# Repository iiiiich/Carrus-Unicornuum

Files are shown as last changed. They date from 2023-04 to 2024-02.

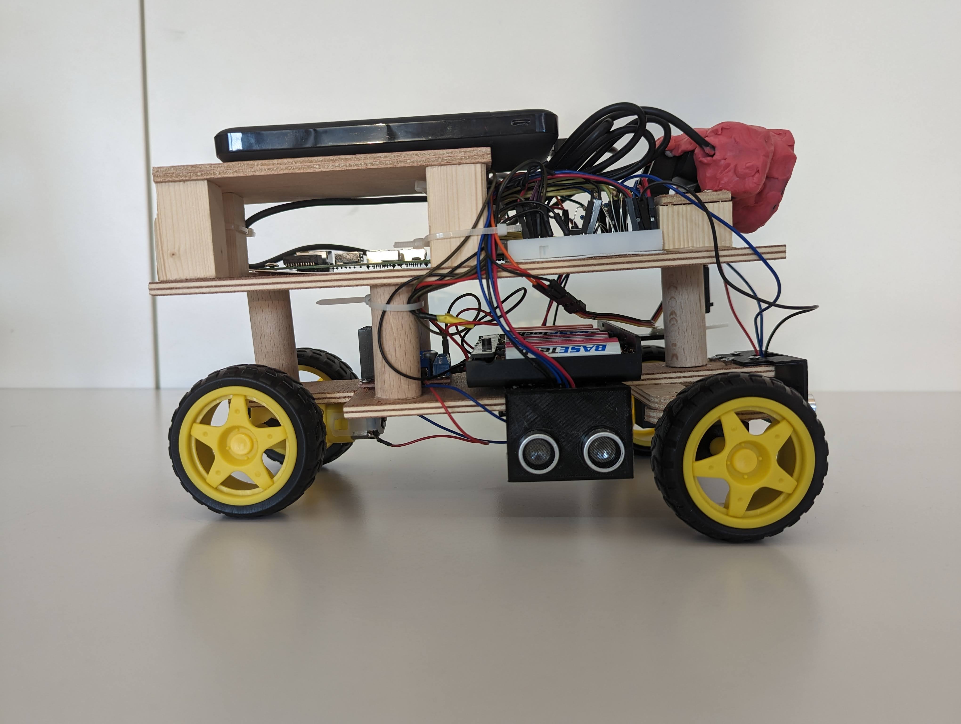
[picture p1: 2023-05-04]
Roboterauto/Ansicht rechts.JPG

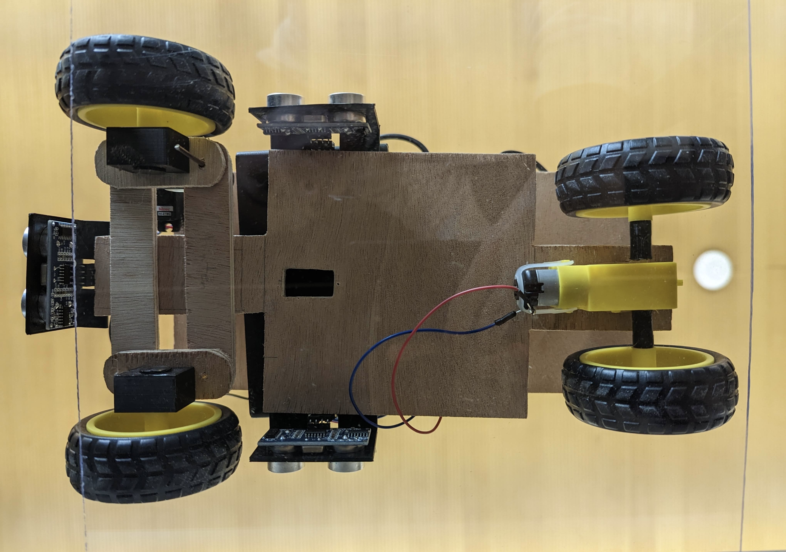
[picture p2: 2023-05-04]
Roboterauto/Ansicht unten.jpg

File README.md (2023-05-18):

# Carrus Unicornuum
World Robot Olympiad 2023 Future Engineers

## Ordnerstruktur
- Im Ordner `3D-Modelle` befindet sich eine .step-Datei, in der alle 3D-Modelle von 3D-gedruckten Komponenten des Roboters zu finden sind.
- Im Ordner `Programmcode` befindet sich der Code, der vom Roboter zum autonomen Fahren verwendet wird, sowie anderer Code, der zur Umsetzung benötigt wird.
- Im Ordner `Roboterauto` befinden sich sechs Fotos des Roboters, die ihn von allen Seiten zeigen.
- Im Ordner `Schaltpläne` befindet sich ein Schaltplan, auf dem zu erkenn ist, wie die einzelnen Komponenten miteinander verbunden sind.
- Im Ordner `Technische Zeichnungen` befinden sich technische Zeichnungen von 3D-gedruckten Komponenten des Roboterautos.
- Im Ordner `Video` befinden sich zwei Links zu YouTube-Videos, die den Roboter bei der autonomen Fahrt sowohl beim Eröffnungs- als auch beim Hindernisrennen zeigen.

## Hardware
### Motorisierung
Der Antrieb des Roboterautos geschieht durch einen DC-Motor. Dieser ist über ein Getriebe mit der Hinterachse und somit mit den Rädern verbunden. Die Lenkung geschieht unabhängig vom Antrieb mit Hilfe eines Servo-Motors des Typs HS-81MG und läuft über die Vorderachse. Alle Motoren sind mit einem Motortreiber L298N verbunden. Dieser regelt die Stromversorgung der Motoren.

### Energie
Die Energieversorgung des Roboterautos geschieht über zwei Einheiten. Zum einen wird der Motortreiber von einer Batterie-Box mit 8 Batterien des Typs AA betrieben. Der Raspberry Pi wird hingegen von einer Powerbank (5V, 3A out; ca. 10.000 mAh) mit Strom versorgt.

### Sensoren
Das Roboter-Auto verfügt neben einer Kamera mit Weitwinkellinse auch über 3 Ultraschallsensoren (HC-SR04), welche dazu dienen, den Abstand nach vorne und zu den Wänden zu bemessen. Somit kann die Lage des Roboterautos innerhalb des Parcours ermittelt werden. Die Kamera hingegen bestimmt den Abstand und die Farbe von Hindernissen.  

## Software
### Eröffnungsrennen
#### Kurven
Flussdiagramm zum Kurvenfahren
#### Korrekturen
Flussdiagramm zum Korrigieren

### Hindernisrennen
Flussdiagramm zur Hindernisumfahrung

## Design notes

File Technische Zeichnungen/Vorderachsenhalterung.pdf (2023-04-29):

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

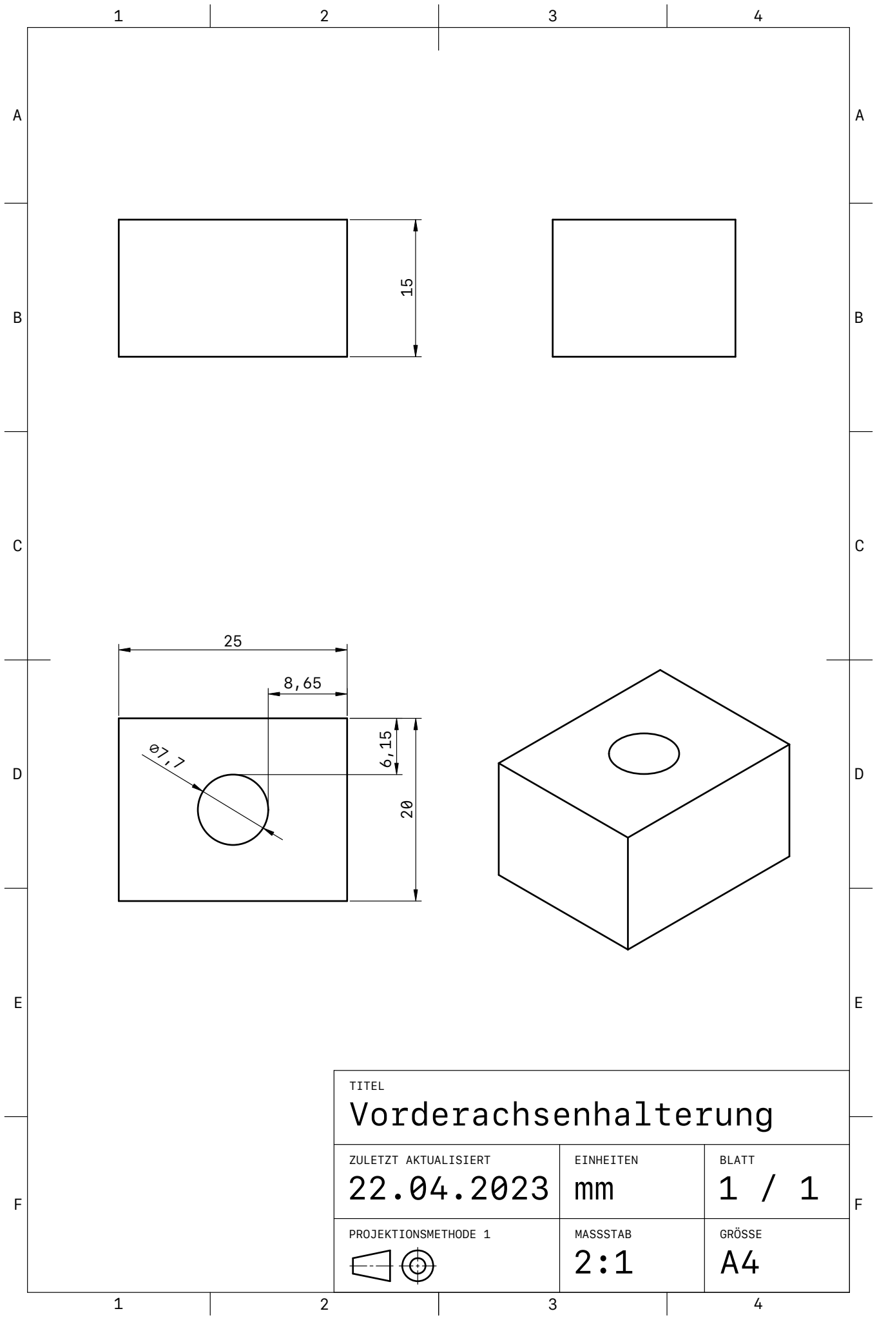
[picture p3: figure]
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

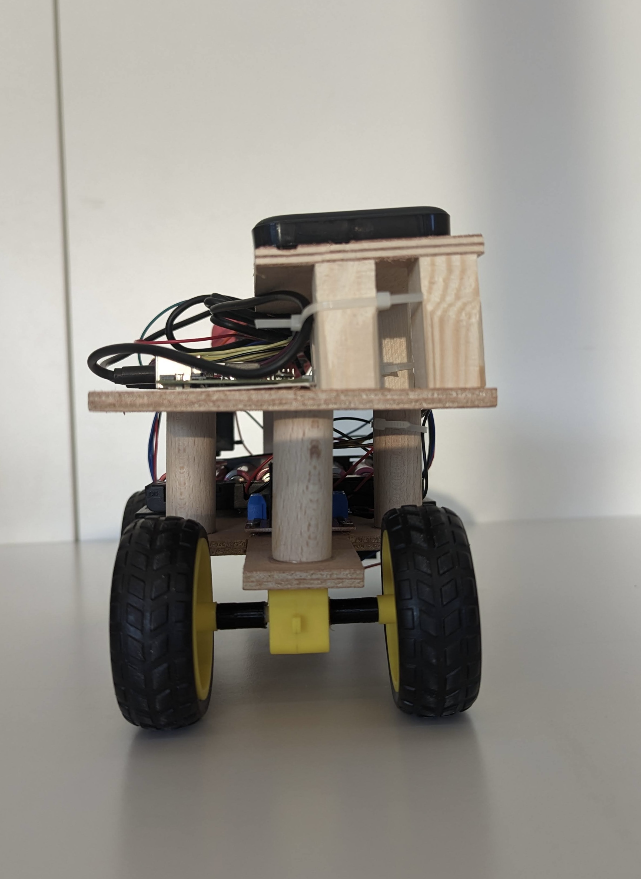
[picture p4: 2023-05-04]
Roboterauto/Ansicht hinten.jpg

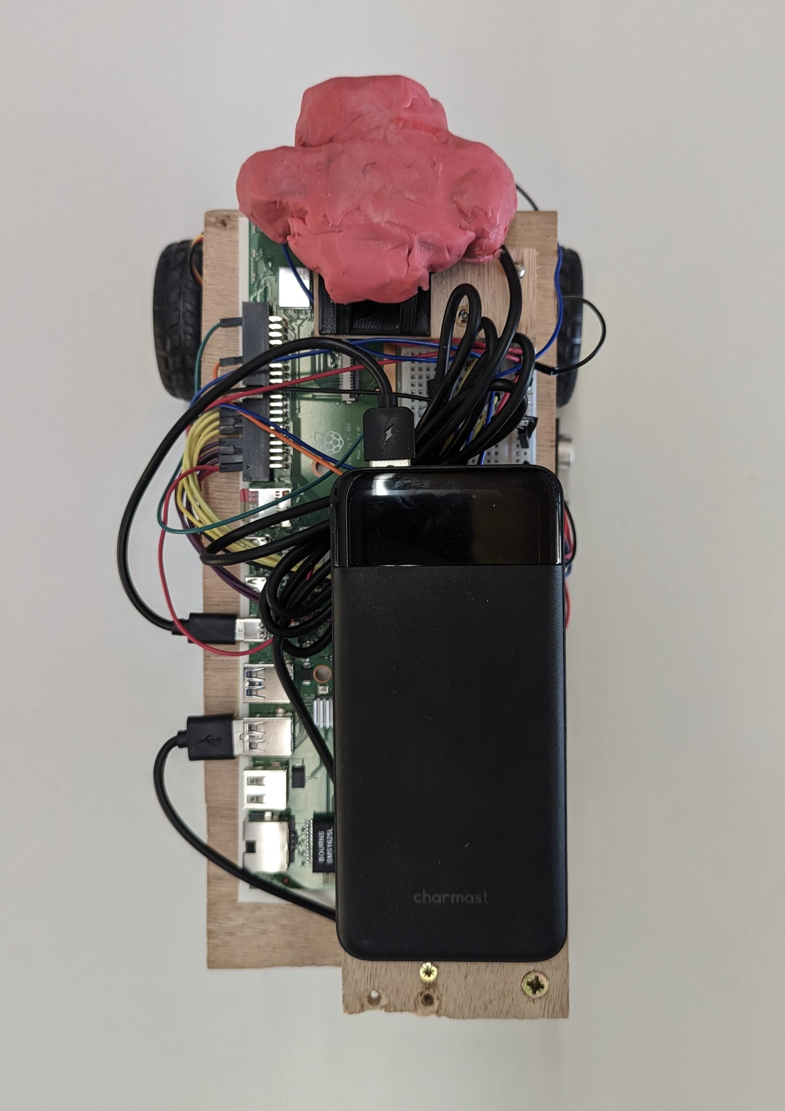
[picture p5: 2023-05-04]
Roboterauto/Ansicht oben.jpg

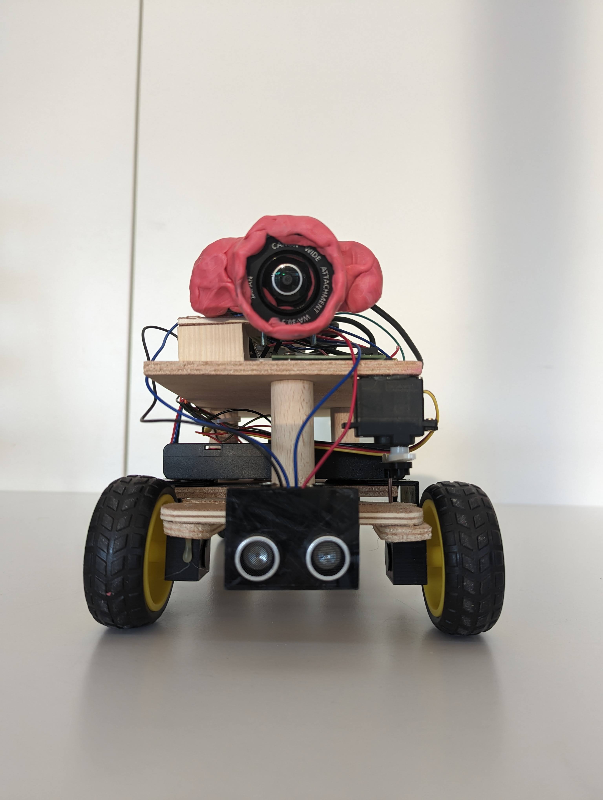
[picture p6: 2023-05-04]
Roboterauto/Ansicht vorne.JPG

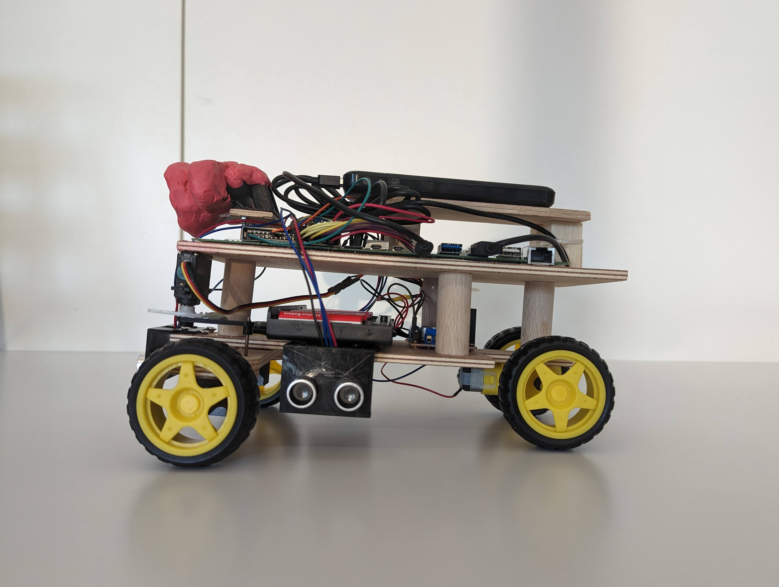
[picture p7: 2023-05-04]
Roboterauto/Ansicht links.JPG

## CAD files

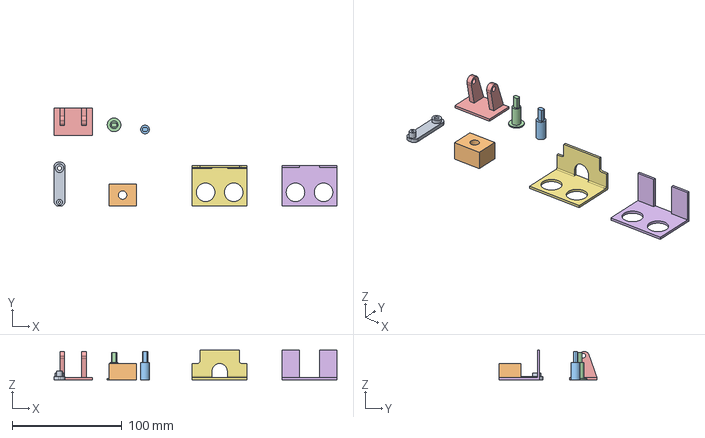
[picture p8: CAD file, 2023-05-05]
3D-Modelle/3D-Modelle.step
257.5 x 89.3 x 27.0 mm

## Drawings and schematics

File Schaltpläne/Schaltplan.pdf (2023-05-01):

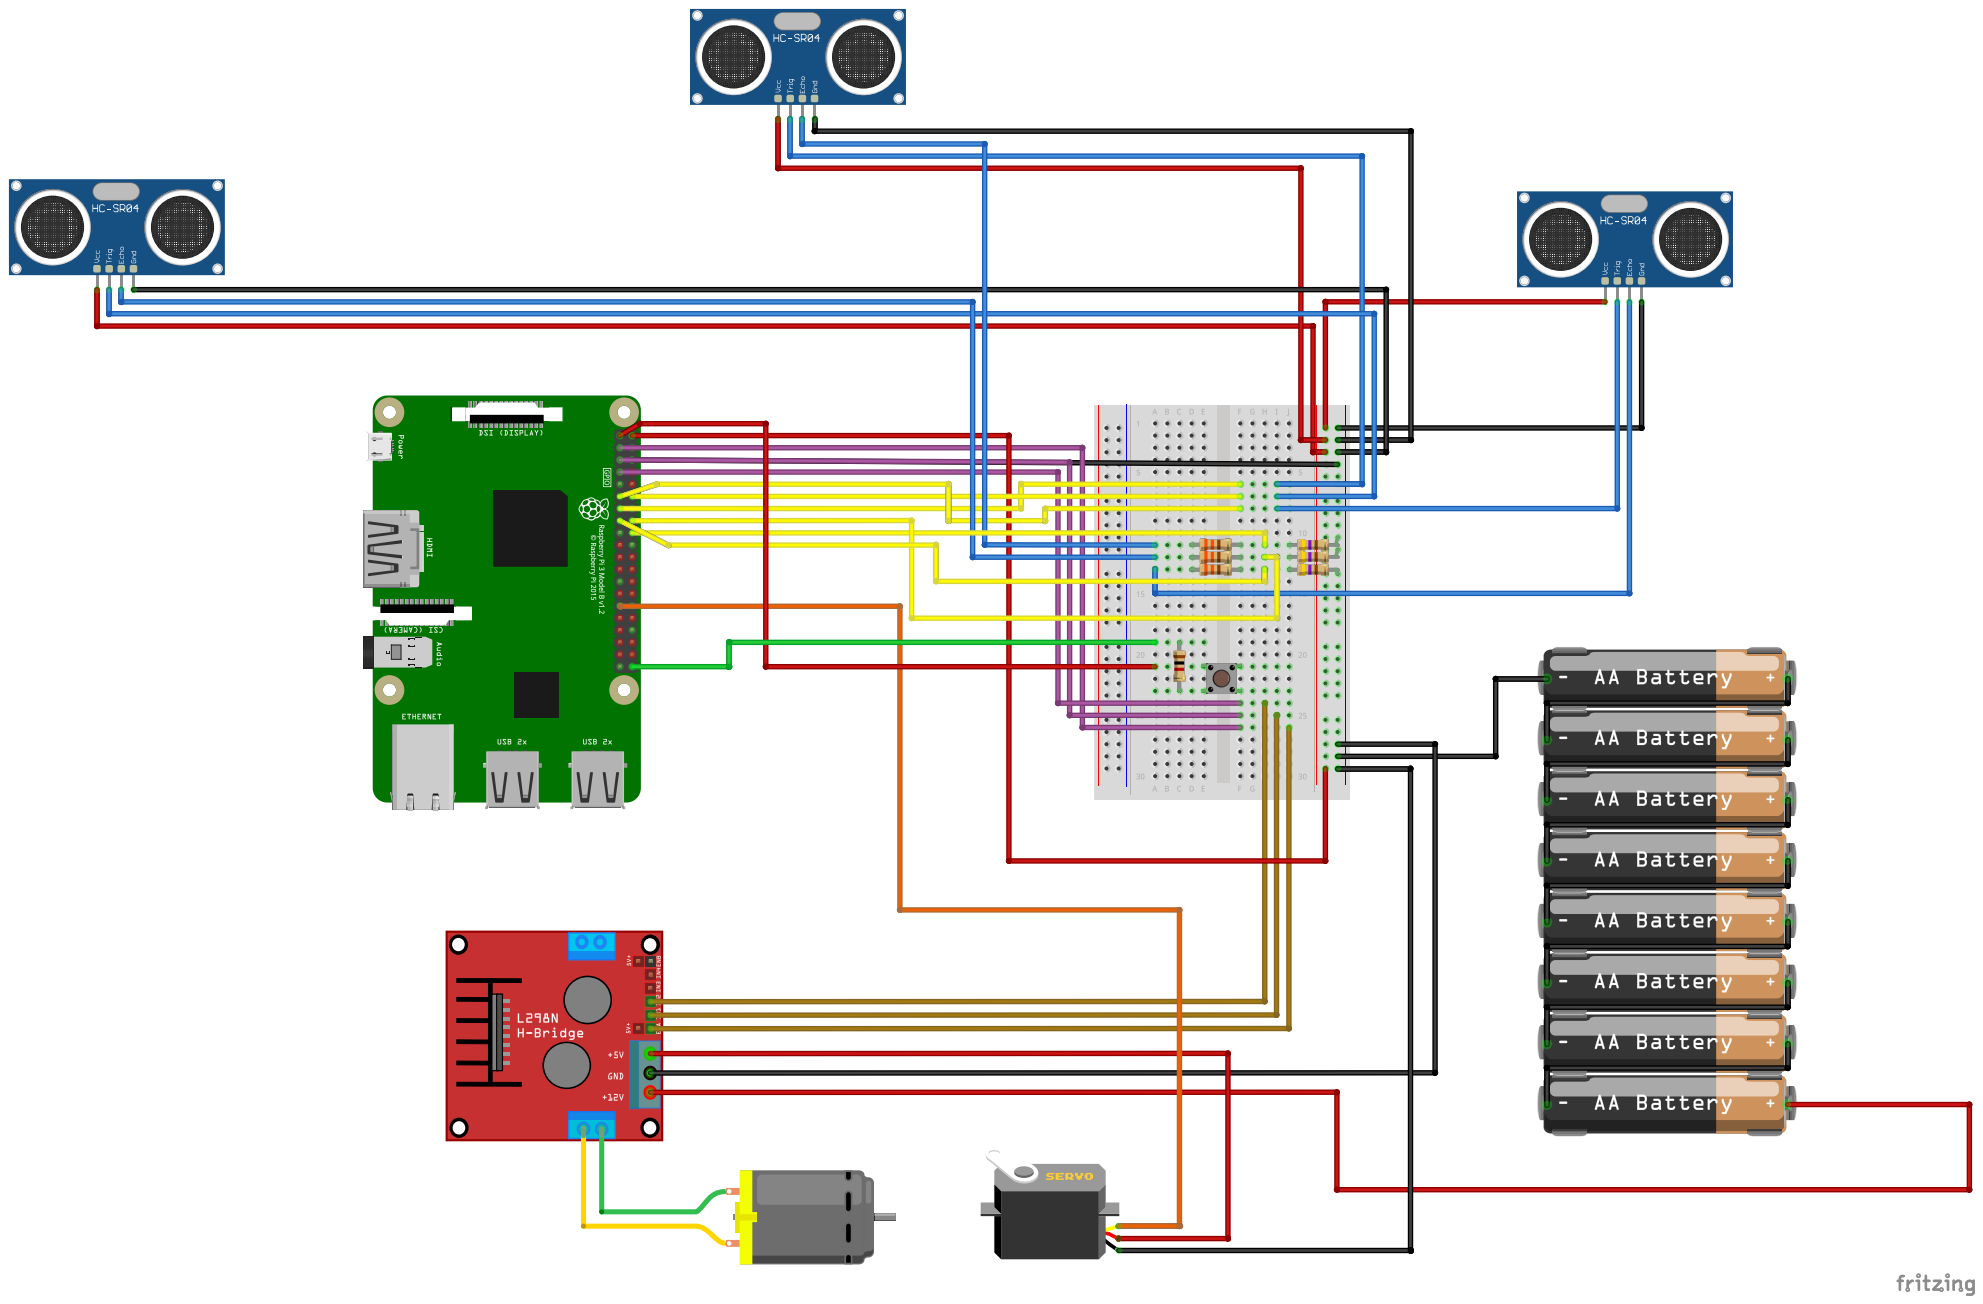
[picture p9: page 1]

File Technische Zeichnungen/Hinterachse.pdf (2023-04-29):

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

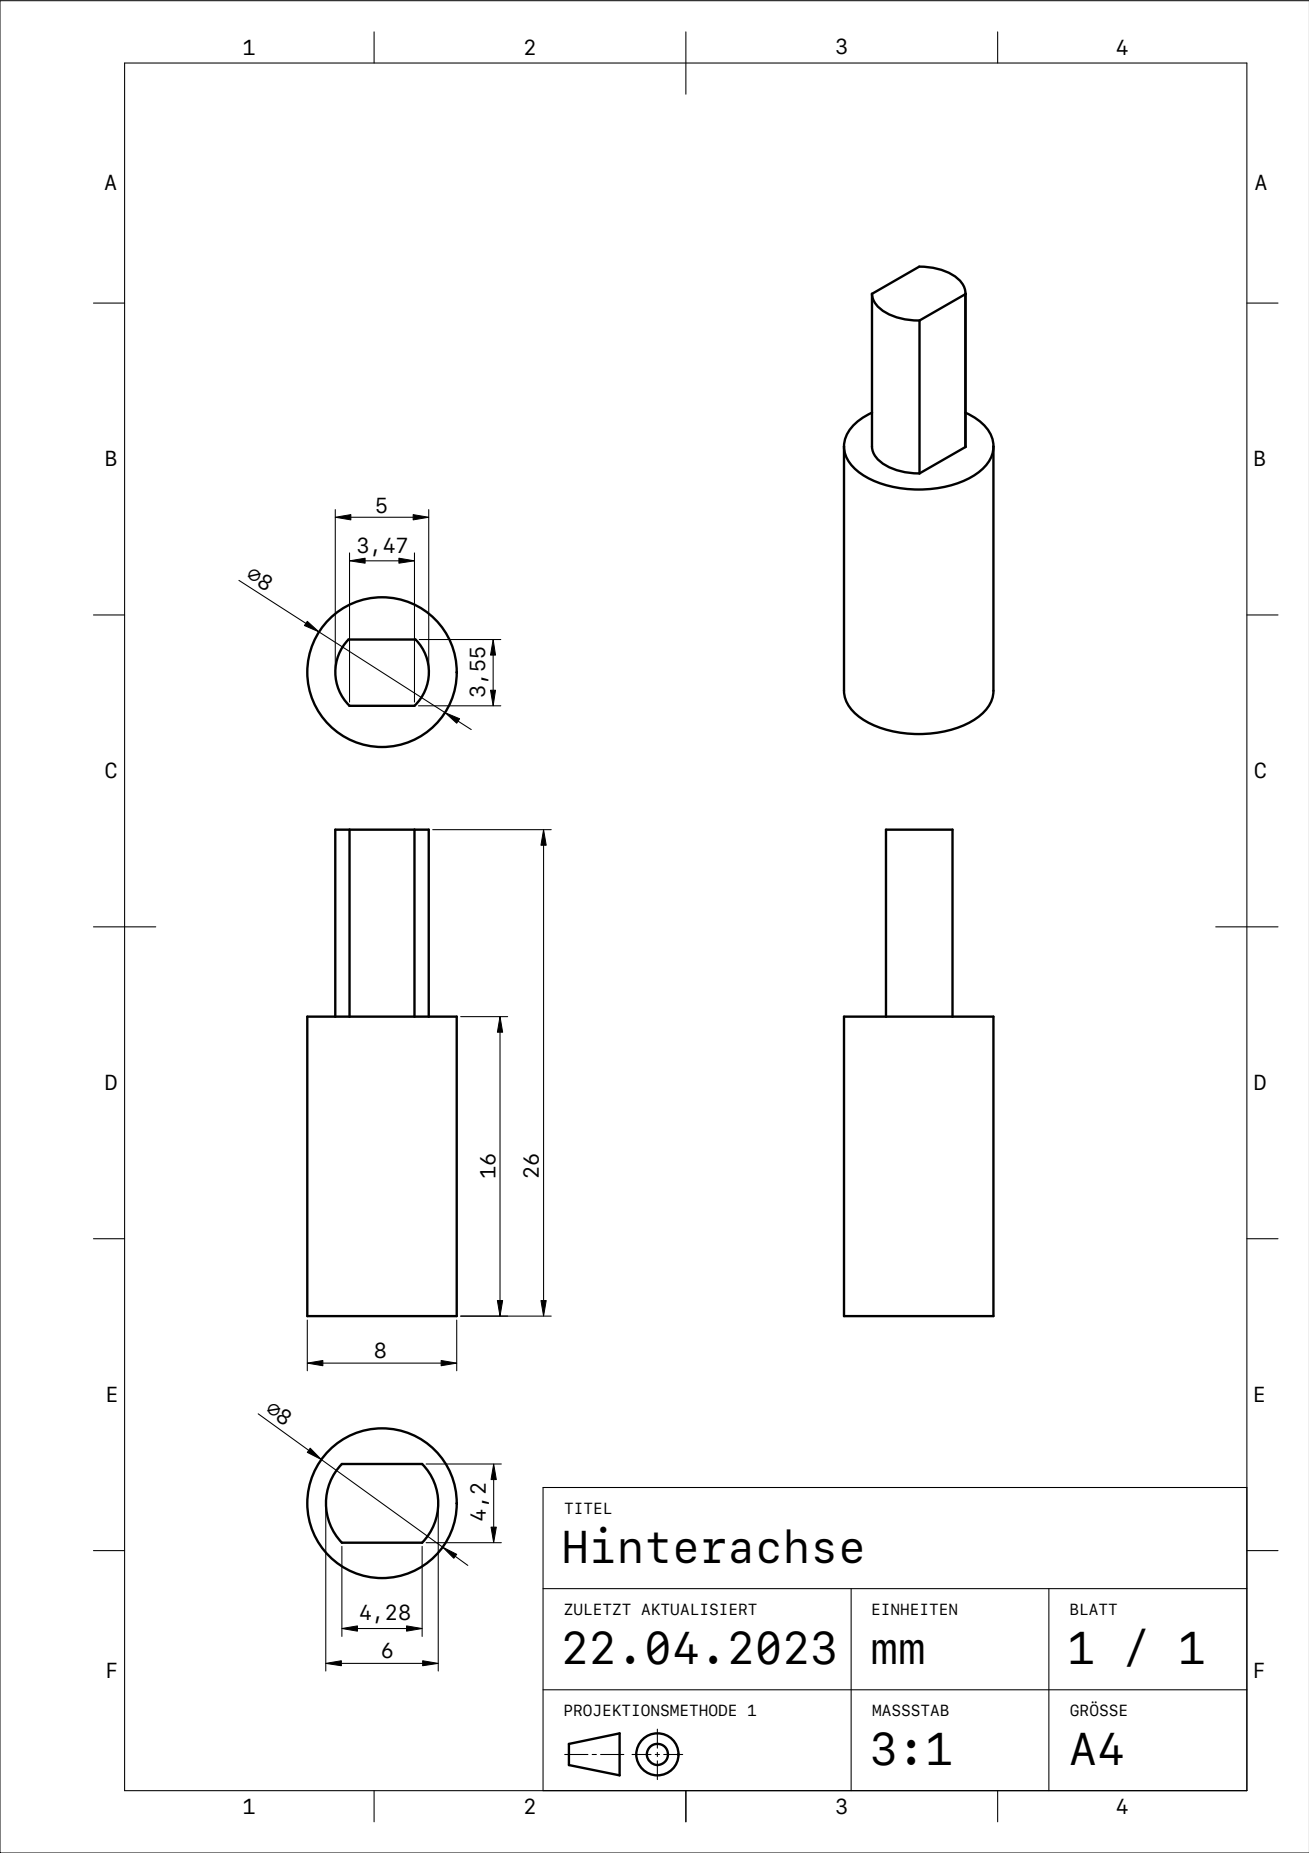
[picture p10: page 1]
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

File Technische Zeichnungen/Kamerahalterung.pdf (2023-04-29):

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

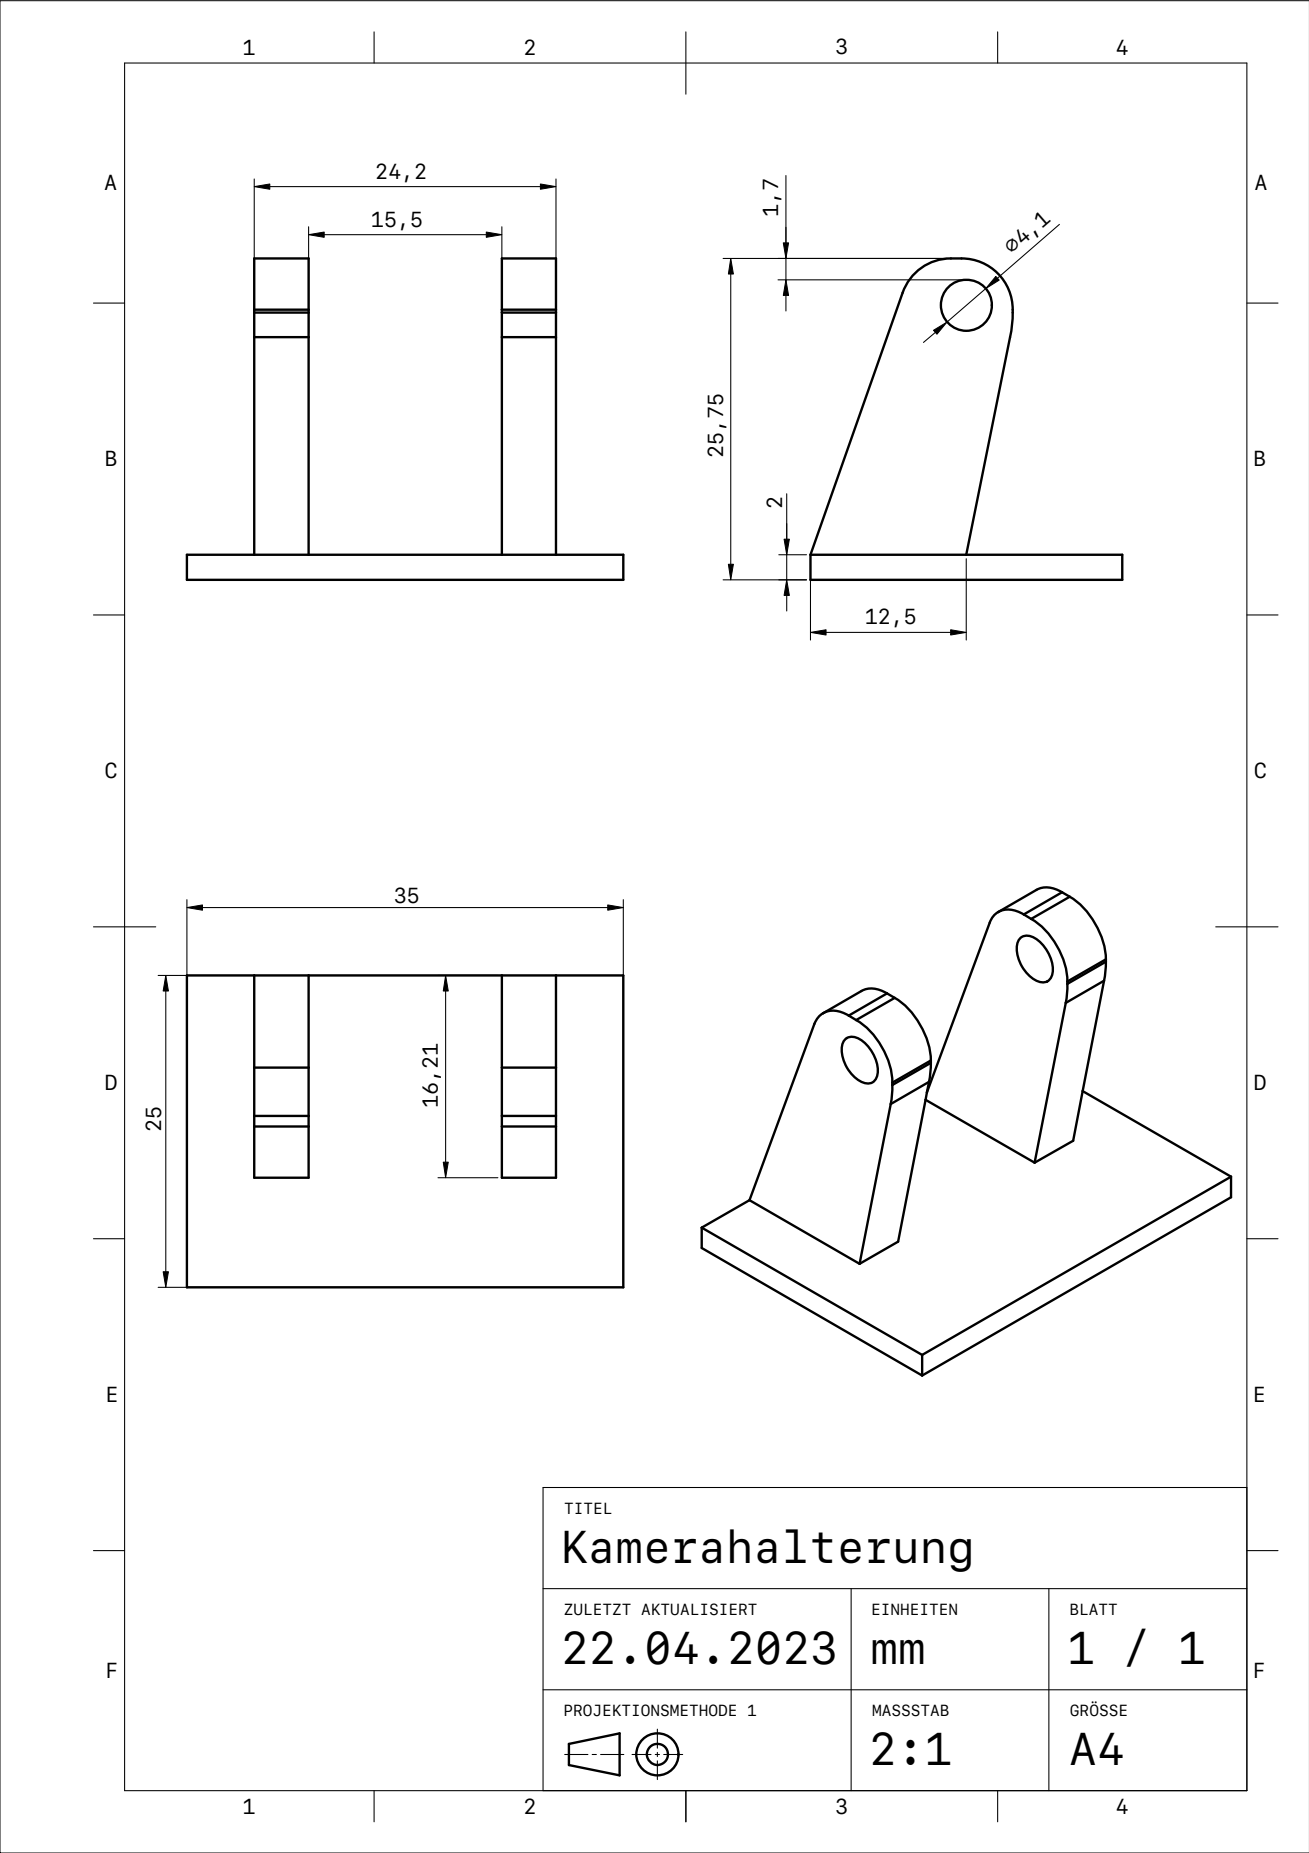
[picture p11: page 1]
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

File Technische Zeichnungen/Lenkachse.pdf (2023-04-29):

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

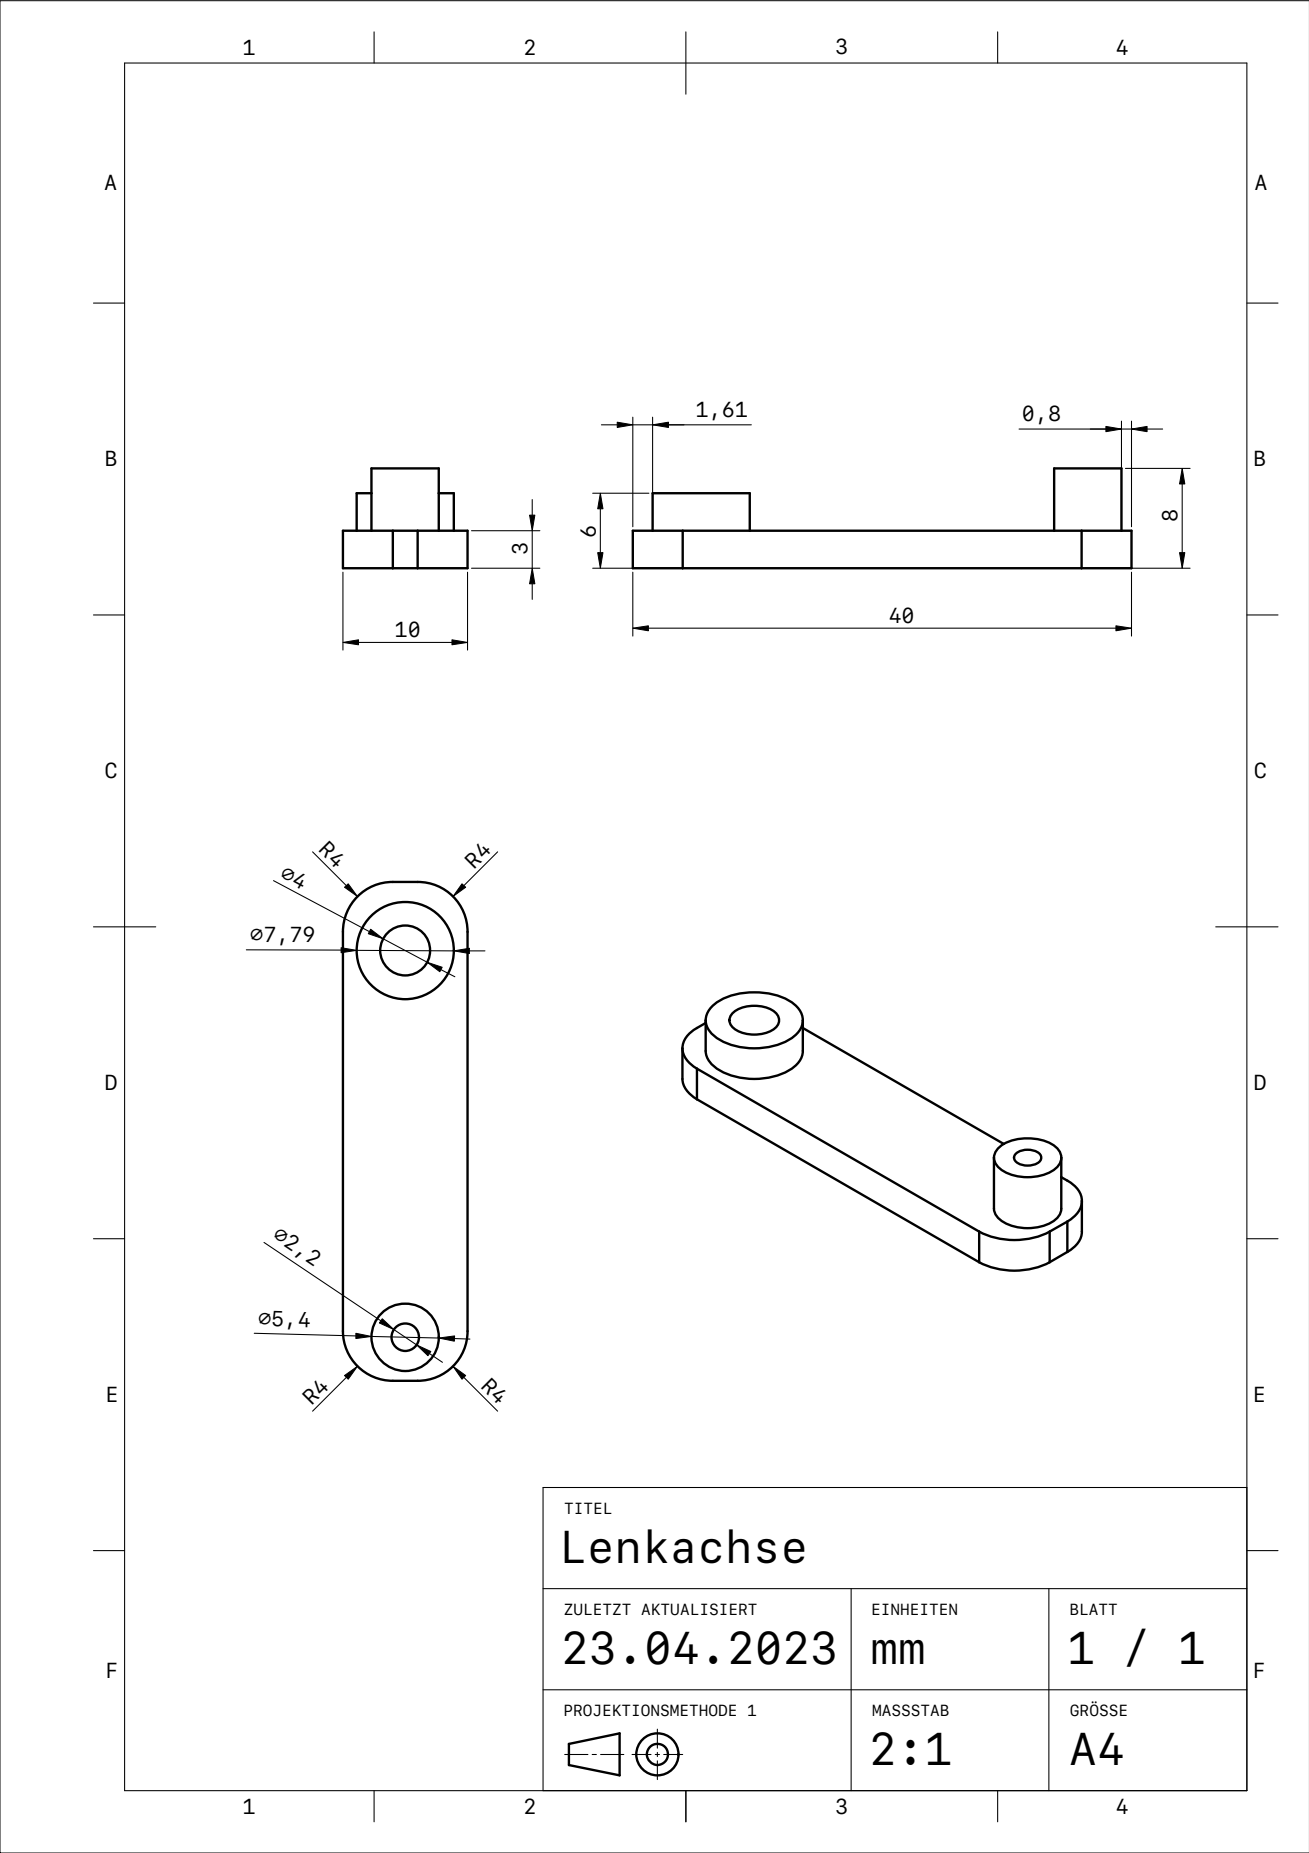
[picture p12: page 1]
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

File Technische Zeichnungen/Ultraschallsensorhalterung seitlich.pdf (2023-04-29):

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

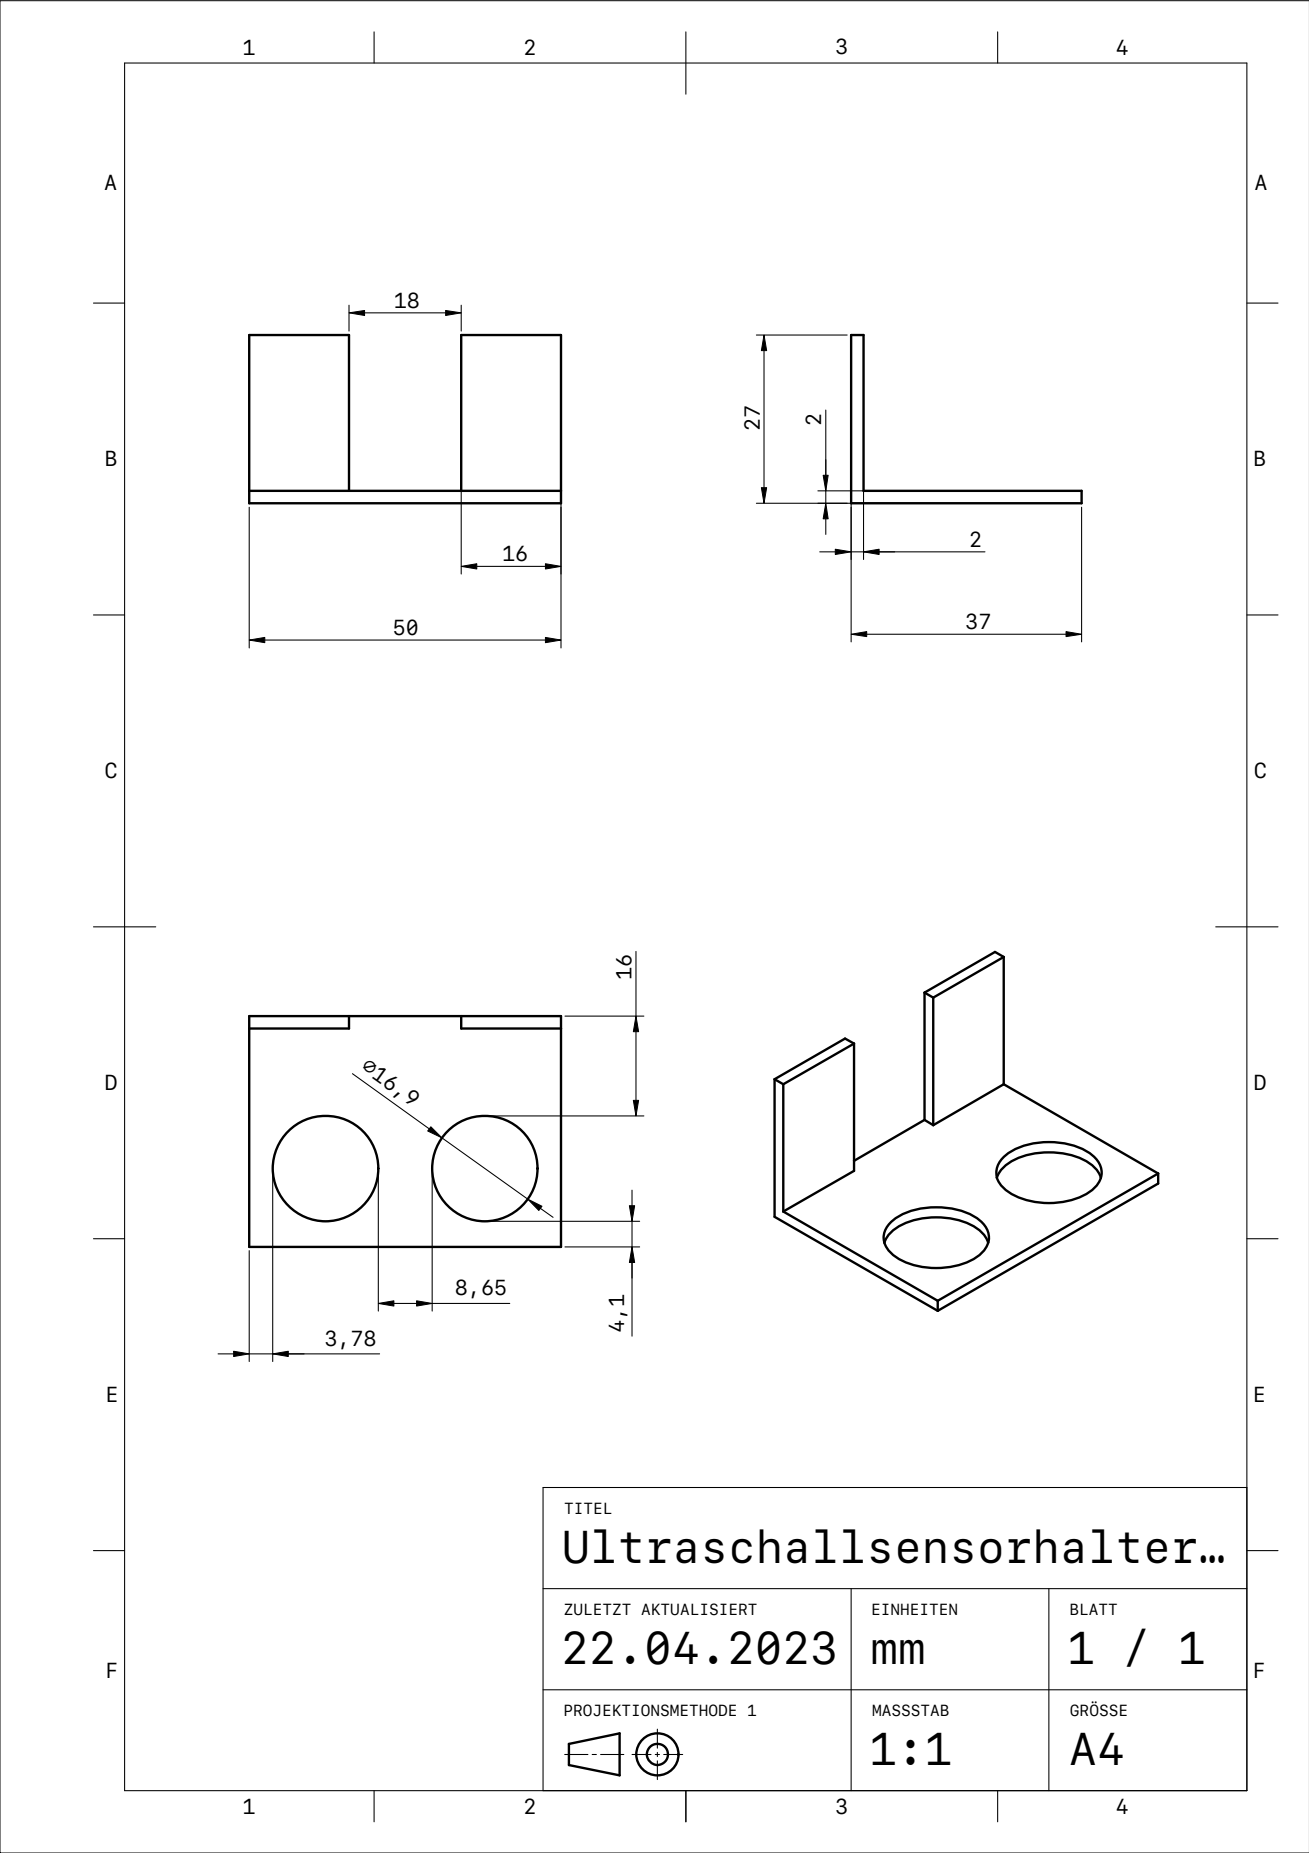
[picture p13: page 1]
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

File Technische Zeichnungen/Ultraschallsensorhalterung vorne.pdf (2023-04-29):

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

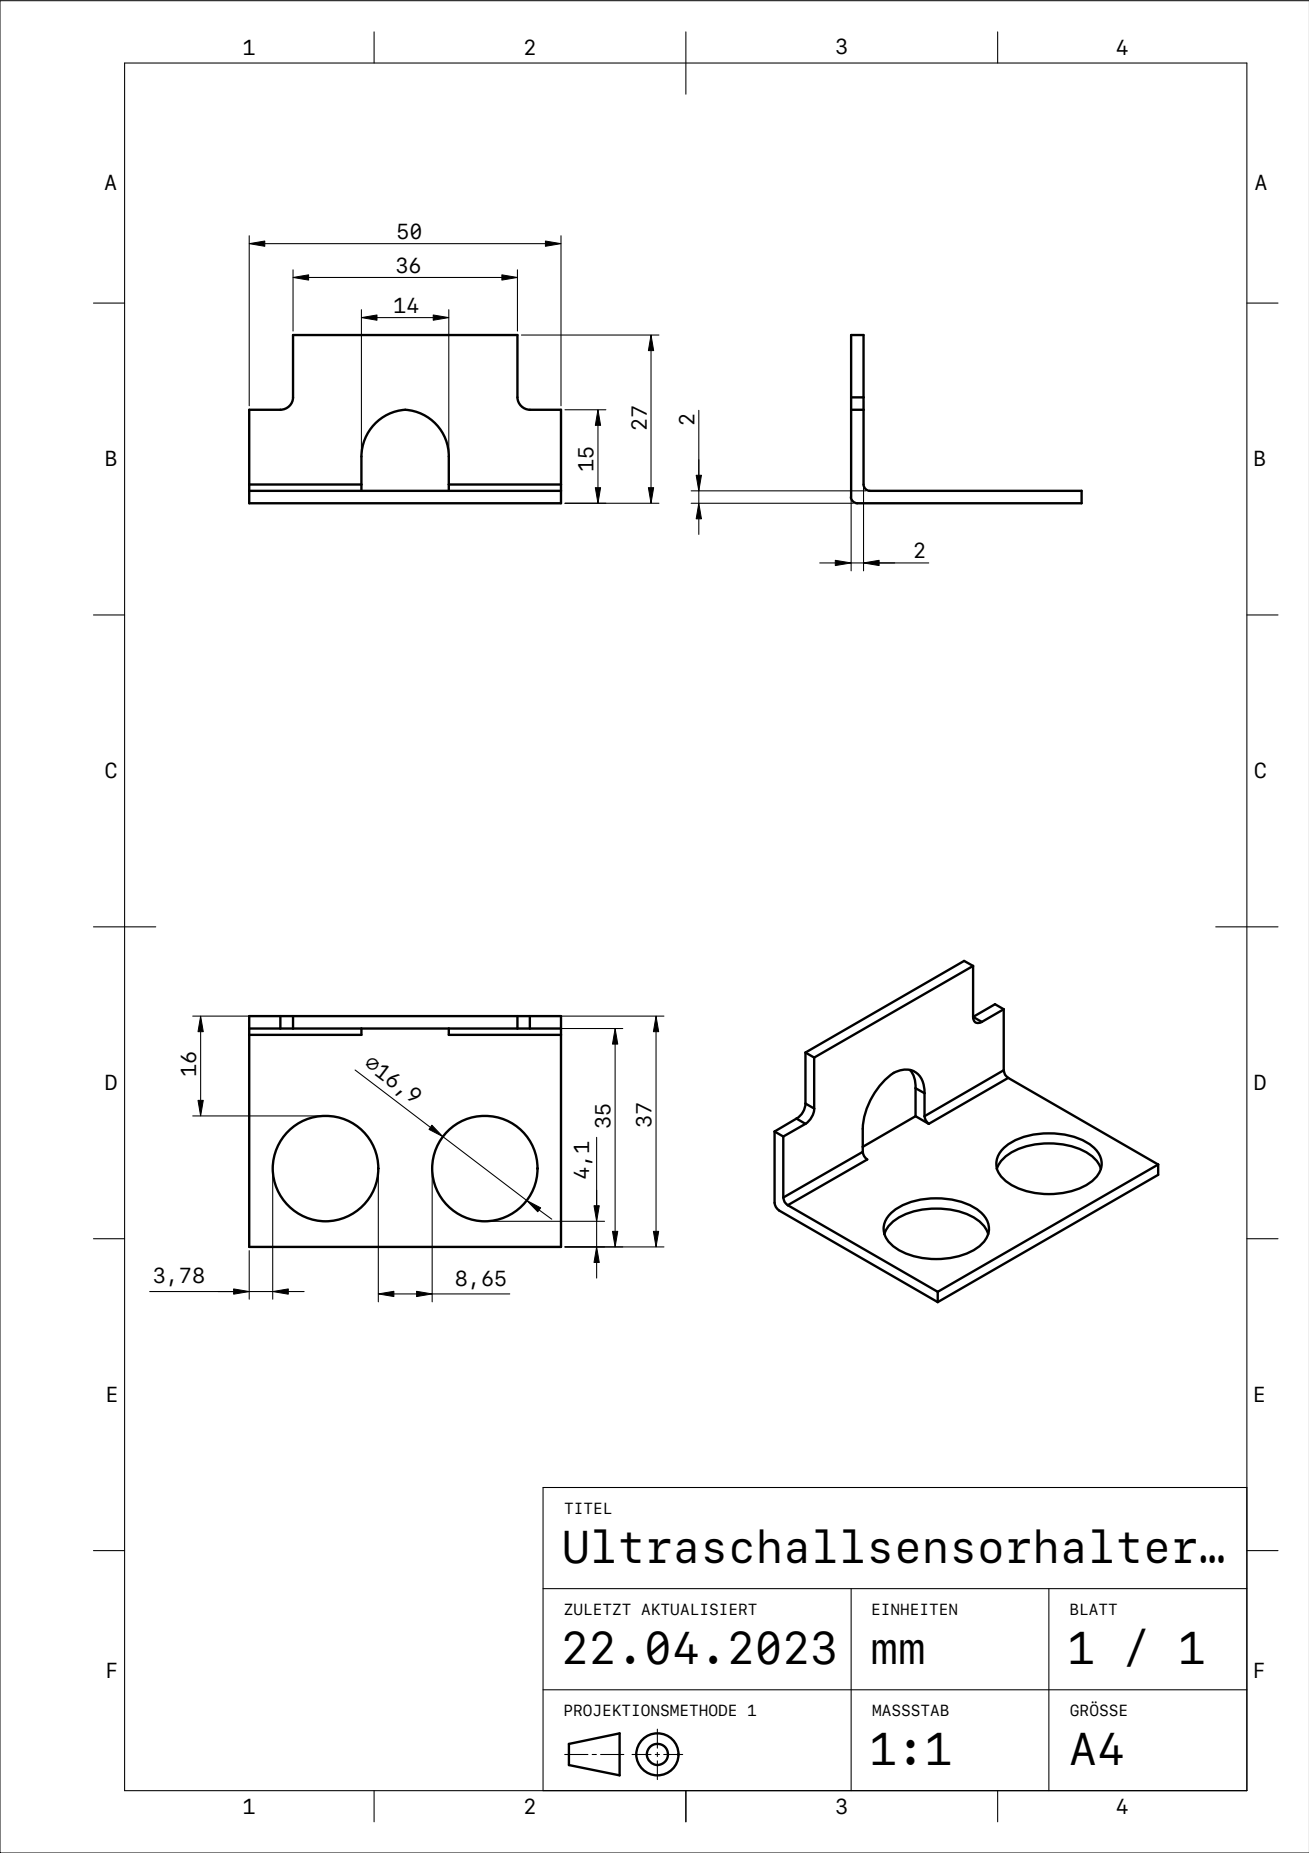
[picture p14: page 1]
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

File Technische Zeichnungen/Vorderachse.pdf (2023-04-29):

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

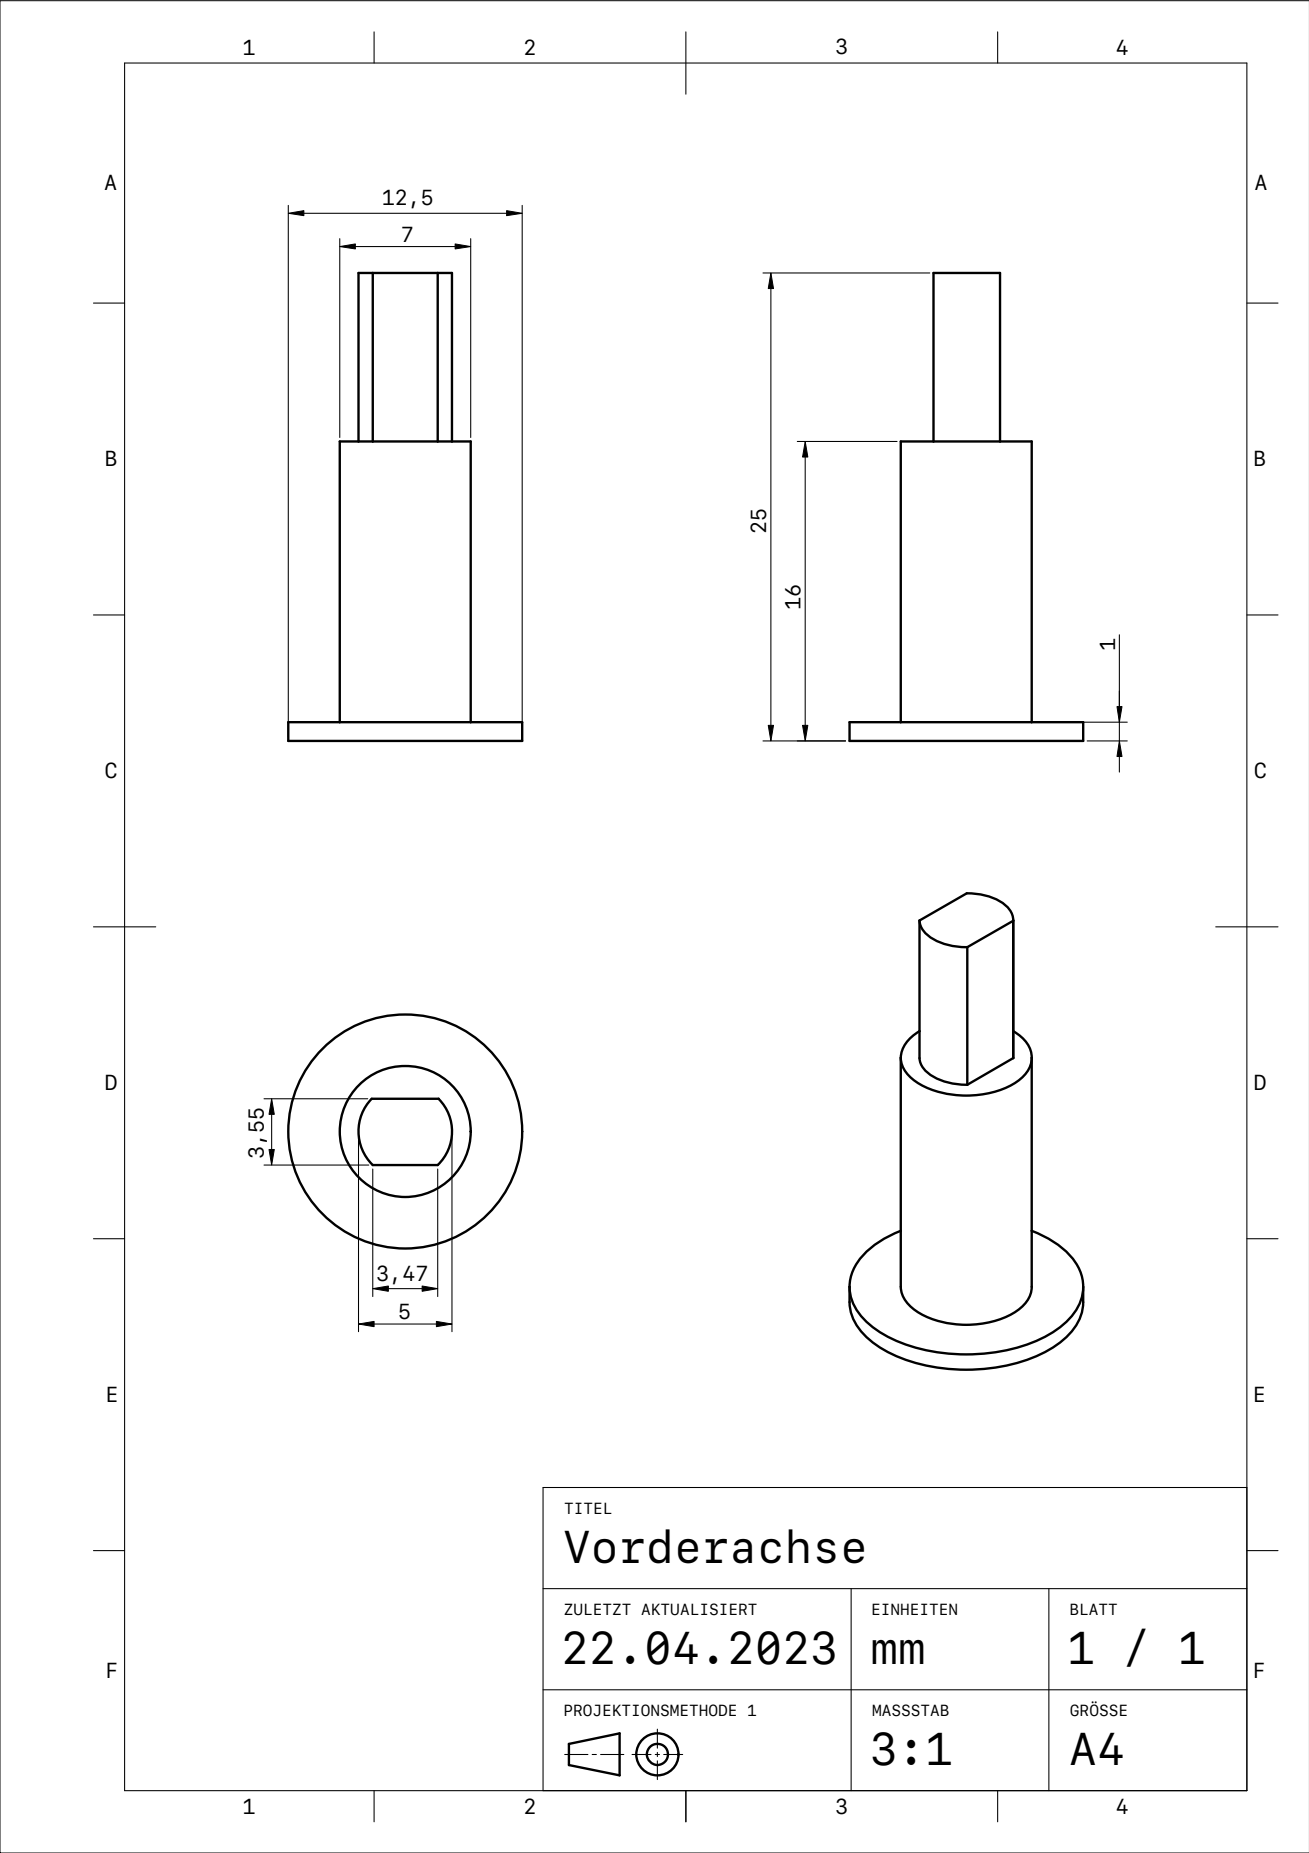
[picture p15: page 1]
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

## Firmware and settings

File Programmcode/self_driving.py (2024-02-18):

import math
import time

import RPi.GPIO as GPIO
import cv2 as cv
import numpy as np


GPIO.setmode(GPIO.BOARD)
GPIO.setwarnings(False)

speed = 60

# HSV limits for color detection
lower_red = np.array([2, 175, 47])
upper_red = np.array([12, 255, 248])
lower_green = np.array([59, 120, 28])
upper_green = np.array([77, 255, 148])

# Variables for camera distance calculation
known_height = 100
focal_length = 567.0

# GPIO pin assignments for button, motors and ultrasonic distance sensors
button_pin = 40
ena, in1, in2 = 3, 5, 7
servo = 29
trig_front, echo_front = 13, 18
trig_right, echo_right = 11, 15
trig_left, echo_left = 12, 16

GPIO.setup(button_pin, GPIO.IN, pull_up_down=GPIO.PUD_DOWN)
# Motor control pins as outputs
GPIO.setup(ena, GPIO.OUT)
GPIO.setup(in1, GPIO.OUT)
GPIO.setup(in2, GPIO.OUT)
# Servo control pin as output
GPIO.setup(servo, GPIO.OUT)
# Ultrasonic sensor pins as outputs (triggers) and inputs (echoes)
GPIO.setup(trig_front, GPIO.OUT)
GPIO.setup(echo_front, GPIO.IN)
GPIO.setup(trig_right, GPIO.OUT)
GPIO.setup(echo_right, GPIO.IN)
GPIO.setup(trig_left, GPIO.OUT)
GPIO.setup(echo_left, GPIO.IN)

# Initialize PWM for motor and servo control
motor_pwm = GPIO.PWM(ena, 100)
motor_pwm.start(0)
servo_pwm = GPIO.PWM(servo, 50)
servo_pwm.start(0)
GPIO.output(in1, GPIO.LOW)
GPIO.output(in2, GPIO.LOW)

# Initialising camera
cap = cv.VideoCapture(0)
if not cap.isOpened():
    print("Cannot open camera")
    exit()


# Function to move forward at a specified speed
def forward(x):
    motor_pwm.ChangeDutyCycle(x)
    GPIO.output(in1, GPIO.HIGH)
    GPIO.output(in2, GPIO.LOW)


# Function to move backward at a specified speed
def backward(x):
    motor_pwm.ChangeDutyCycle(x)
    GPIO.output(in1, GPIO.LOW)
    GPIO.output(in2, GPIO.HIGH)


# Function to stop the motor
def stop():
    GPIO.output(in1, GPIO.LOW)
    GPIO.output(in2, GPIO.LOW)


# Function to steer forward
def steer_forward():
    global steering_direction
    
    if steering_direction == "left":
        servo_pwm.ChangeDutyCycle(7.2)
    elif steering_direction == "right":
        servo_pwm.ChangeDutyCycle(7.4)
    else:
        servo_pwm.ChangeDutyCycle(7.3)
    steering_direction = "forward"


# Function to steer left
def steer_left():
    global steering_direction
    
    servo_pwm.ChangeDutyCycle(9.3)
    steering_direction = "left"


# Function to steer right
def steer_right():
    global steering_direction
    
    servo_pwm.ChangeDutyCycle(5.3)
    steering_direction = "right"


# Function to get measurements from ultrasonic distance sensors
def ultrasonic_distance_measurement():
    # Initialising variables for ultrasonic distance measurement
    pulse_start_front, pulse_end_front, pulse_duration_front = time.time(), time.time(), 0
    pulse_start_right, pulse_end_right, pulse_duration_right = time.time(), time.time(), 0
    pulse_start_left, pulse_end_left, pulse_duration_left = time.time(), time.time(), 0
    global distance_front_measured, distance_right_measured, distance_left_measured

    # Triggering ultrasonic distance sensors
    GPIO.output(trig_front, GPIO.LOW)
    GPIO.output(trig_right, GPIO.LOW)
    GPIO.output(trig_left, GPIO.LOW)
    time.sleep(0.02)

    # Getting front distance
    GPIO.output(trig_front, GPIO.HIGH)
    time.sleep(0.00001)
    GPIO.output(trig_front, GPIO.LOW)
    trig_start_time = time.time()
    while GPIO.input(echo_front) == 0:
        pulse_start_front = time.time()
        if (time.time() - trig_start_time) >= 0.2:
            pulse_start_front = -1
            break
    while GPIO.input(echo_front) == 1:
        pulse_end_front = time.time()
        if (time.time() - trig_start_time) >= 0.2:
            pulse_end_front = -2
            break
    pulse_duration_front = pulse_end_front - pulse_start_front
    distance_front_measured = pulse_duration_front * 17150
    distance_front_measured = round(distance_front_measured, 2)

    # Getting right distance
    GPIO.output(trig_right, GPIO.HIGH)
    time.sleep(0.00001)
    GPIO.output(trig_right, GPIO.LOW)
    trig_start_time = time.time()
    while GPIO.input(echo_right) == 0:
        pulse_start_right = time.time()
        if (time.time() - trig_start_time) >= 0.2:
            pulse_start_right = -1
            break
    while GPIO.input(echo_right) == 1:
        pulse_end_right = time.time()
        if (time.time() - trig_start_time) >= 0.2:
            pulse_end_right = -2
            break
    pulse_duration_right = pulse_end_right - pulse_start_right
    distance_right_measured = pulse_duration_right * 17150
    distance_right_measured = round(distance_right_measured, 2)

    # Getting left distance
    GPIO.output(trig_left, GPIO.HIGH)
    time.sleep(0.00001)
    GPIO.output(trig_left, GPIO.LOW)
    trig_start_time = time.time()
    while GPIO.input(echo_left) == 0:
        pulse_start_left = time.time()
        if (time.time() - trig_start_time) >= 0.2:
            pulse_start_left = -1
            break
    while GPIO.input(echo_left) == 1:
        pulse_end_left = time.time()
        if (time.time() - trig_start_time) >= 0.2:
            pulse_end_left = -2
            break
    pulse_duration_left = pulse_end_left - pulse_start_left
    distance_left_measured = pulse_duration_left * 17150
    distance_left_measured = round(distance_left_measured, 2)


# Function to get the height and x-coordinate in the frame of the biggest object within the HSV limits
def obj_data(frame, lower, upper, color):
    x, w, h = 400, 0, 0
    min_area = 600
    hsv = cv.cvtColor(frame, cv.COLOR_BGR2HSV)
    mask = cv.inRange(hsv, lower, upper)
    _, mask1 = cv.threshold(mask, 254, 255, cv.THRESH_BINARY)
    contours, _ = cv.findContours(mask1, cv.RETR_EXTERNAL, cv.CHAIN_APPROX_NONE)
    for contour in contours:
        if cv.contourArea(contour) > min_area:
            x, y, w, h = cv.boundingRect(contour)
            cv.rectangle(frame, (x, y), (x + w, y + h), color, 2)
            min_area = cv.contourArea(contour)
    return (x + w / 2), h


# Function to calculate the distance of an object in the camera frame
def distance_calculation(focal_length, known_height, obj_height_in_frame):
    distance = (known_height * focal_length) / obj_height_in_frame
    horizontal_distance = math.sqrt(distance ** 2 - 81 ** 2)
    return horizontal_distance
    

steering_direction = ""

stop()
steer_forward()
time.sleep(0.1)
servo_pwm.ChangeDutyCycle(0)

if __name__ == "__main__":
    while True:
        # Initialising variables
        last_distance_front, last_distance_right, last_distance_left = 0, 0, 0
        distances_front, distances_right, distances_left = [], [], []
        distance_front_measured, distance_right_measured, distance_left_measured = 0, 0, 0
        corner_counter = 0
        distance_measurement_is_up_to_date = False
        last_distance_measurement_time, current_distance_measurement_time = time.time(), time.time()
        distance_right_change, distance_left_change = 0, 0
        steering_blocked, steering_blocked2 = False, False
        measurement_counter = 0
        is_running = False
        has_increased, has_decreased = False, False
        steering_direction = ""
        script_start_time = time.time()
        has_corrected_left, has_corrected_right = False, False
        steering_end_time = time.time()
        distance_front_change = 0
        stopping_enabled, stopping_enabled_time = False, time.time()
        red_obj_x, green_obj_x = 0, 0
        distance_nearest_obstacle = 0
        nearest_obstacle_x = 400
        nearest_obstacle_color = ""
        avoiding_red_obstacle, avoiding_green_obstacle = False, False
        avoiding_start_time = time.time()
        avoiding_distance = 0
        is_obstacle_race = False
        frame_counter = 0
        just_avoided_obstacle, just_avoided_obstacle2 = False, False
        avoiding_end_time = time.time()
        avoiding_duration = 0
        avoiding_color = ""
        avoiding_allowed = True
        corner_direction = ""
        corner_allowed = True
        backward_time = script_start_time
        pulse_start_front, pulse_end_front, pulse_duration_front = time.time(), time.time(), 0
        pulse_start_right, pulse_end_right, pulse_duration_right = time.time(), time.time(), 0
        pulse_start_left, pulse_end_left, pulse_duration_left = time.time(), time.time(), 0
        distance_front, distance_right, distance_left = 0, 0, 0
        steering_start_time = time.time()
        red_obj_height_in_frame, green_obj_height_in_frame = 0, 0
        distance_red, distance_green = 0, 0
        just_stopped_corner_turn_because_of_obstacle = False
        max_distance_front = 0
        
        steeringDirectionInt = 75

        while True:
            # Starting if button is pressed
            if GPIO.input(button_pin) == GPIO.HIGH:
                is_running = True
                steer_forward()
                time.sleep(0.5)
                forward(speed)
                script_start_time = time.time()
                frame_start_time = time.time()
                break

        while is_running:
            has_corrected_left = False
            has_corrected_right = False
        

            # Stopping if button is pressed
            if GPIO.input(button_pin) == GPIO.HIGH and (time.time() - script_start_time) > 2:
                is_running = False
                steer_forward()
                stop()
                time.sleep(0.2)
                servo_pwm.ChangeDutyCycle(0)
                break

            # Getting measurements from ultrasonic distance sensors
            ultrasonic_distance_measurement()

            # Taking each three measurements from the ultrasonic distance sensors and forming the median of these
            if 0 < distance_front_measured < 350:
                distances_front.append(distance_front_measured)
                distance_measurement_is_up_to_date = False
            if 0 < distance_right_measured < 350:
                distances_right.append(distance_right_measured)
            if 0 < distance_left_measured < 350:
                distances_left.append(distance_left_measured)
            if len(distances_front) == 3:
                distances_front.sort()
                last_distance_front = distance_front
                distance_front = round(distances_front[1], 2)
                distances_front = []
                distance_measurement_is_up_to_date = True
                last_distance_measurement_time = current_distance_measurement_time
                current_distance_measurement_time = time.time()
            if len(distances_right) == 3:
                distances_right.sort()
                last_distance_right = distance_right
                distance_right = round(distances_right[1], 2)
                distances_right = []
            if len(distances_left) == 3:
                distances_left.sort()
                last_distance_left = distance_left
                distance_left = round(distances_left[1], 2)
                distances_left = []
            
            # Waiting until a new median of the measurements of the ultrasonic distance sensors is formed before allowing steering again
            if measurement_counter > 0:
                measurement_counter += 1
                if measurement_counter >= 4 and (time.time() - steering_start_time) >= 0.5:
                    measurement_counter = 0
                    steering_blocked2 = False
            
            # Reading camera image
            success, frame = cap.read()
            if not success:
                print("Can't receive frame. Exiting ...")
                break

            # Cropping camera image
            frame = frame[80:, 0:]

            # Calculating the distances to the nearest red and the nearest green obstacle
            red_obj_x, red_obj_height_in_frame = obj_data(frame, lower_red, upper_red, (0, 0, 255))
            if red_obj_height_in_frame != 0:
                distance_red = distance_calculation(focal_length, known_height, red_obj_height_in_frame)
                if not is_obstacle_race:
                    is_obstacle_race = True
                    print("Detected obstacle race")
                cv.putText(frame, f"distance: {round((distance_red / 10), 2)} cm", (35, 40), cv.FONT_HERSHEY_SIMPLEX, 0.7, (0, 0, 255), 2)
            else:
                distance_red = 0
            green_obj_x, green_obj_height_in_frame = obj_data(frame, lower_green, upper_green, (0, 255, 0))
            if green_obj_height_in_frame != 0:
                distance_green = distance_calculation(focal_length, known_height, green_obj_height_in_frame)
                if not is_obstacle_race:
                    is_obstacle_race = True
                    print("Detected obstacle race")
                cv.putText(frame, f"distance: {round((distance_green / 10), 2)} cm", (35, 80), cv.FONT_HERSHEY_SIMPLEX, 0.7, (0, 255, 0), 2)
            else:
                distance_green = 0

            # Determining which obstacle is the nearest and its x-coordinate in the frame
            if distance_red == 0 and distance_green == 0:
                distance_nearest_obstacle = 0
                nearest_obstacle_x = 400
                nearest_obstacle_color = ""
            elif distance_red != 0 and distance_green != 0 and distance_red < distance_green:
                distance_nearest_obstacle = distance_red
                nearest_obstacle_x = red_obj_x
                nearest_obstacle_color = "red"
            elif distance_red != 0 and distance_green != 0 and distance_green <= distance_red:
                distance_nearest_obstacle = distance_green
                nearest_obstacle_x = green_obj_x
                nearest_obstacle_color = "green"
            elif distance_red == 0:
                distance_nearest_obstacle = distance_green
                nearest_obstacle_x = green_obj_x
                nearest_obstacle_color = "green"
            else:
                distance_nearest_obstacle = distance_red
                nearest_obstacle_x = red_obj_x
                nearest_obstacle_color = "red"
            
            # Displaying frame (currently not used)
            # cv.imshow("Frame", frame)
            if cv.waitKey(1) & 0xFF == 27:
                break

            # Eventually resetting variables to allow certain actions
            if not just_avoided_obstacle and just_avoided_obstacle2 and distance_measurement_is_up_to_date and (time.time() - avoiding_end_time) >= 0.8:
                just_avoided_obstacle2 = False
            if just_avoided_obstacle and just_avoided_obstacle2 and distance_measurement_is_up_to_date:
                just_avoided_obstacle = False

            if ((time.time() - avoiding_end_time) > 1 or nearest_obstacle_color != avoiding_color or distance_nearest_obstacle > avoiding_distance) and not avoiding_allowed:
                avoiding_allowed = True

            # Making a 90°-turn in the corners
            # Starting corner turn
            if corner_allowed and distance_left > 90 and distance_front < 80 and distance_measurement_is_up_to_date and not steering_blocked and not steering_blocked2 and corner_counter < 12 and (time.time() - steering_end_time) >= 1.5 and corner_direction != "right":
                steering_blocked = True
                steering_blocked2 = True
                print("\nNow steering left\n")
                steer_left()
                measurement_counter = 1
                steering_start_time = time.time()
                if corner_direction == "":
                    corner_direction = "left"
            if corner_allowed and distance_right > 90 and distance_front < 80 and distance_measurement_is_up_to_date and not steering_blocked and not steering_blocked2 and corner_counter < 12 and (time.time() - steering_end_time) >= 1.5 and corner_direction != "left":
                steering_blocked = True
                steering_blocked2 = True
                print("\nNow steering right\n")
                steer_right()
                measurement_counter = 1
                steering_start_time = time.time()
                if corner_direction == "":
                    corner_direction = "right"

            if steering_blocked and not has_increased and round(last_distance_front) < (round(distance_front) - 25) and distance_front >= 100:
                max_distance_front = distance_front
                has_increased = True

            if steering_blocked and has_increased and max_distance_front > (distance_front + 11):
                has_decreased = True

            # Stopping corner turn
            if steering_blocked and has_increased and has_decreased and not steering_blocked2:
                steering_end_time = time.time()
                if steering_direction == "left":
                    steer_forward()
                    print("Steering stopped")
                    has_increased = False
                    has_decreased = False
                    steering_blocked = False
                    corner_counter += 1
                if steering_direction == "right":
                    steer_forward()
                    print("Steering stopped")
                    has_increased = False
                    has_decreased = False
                    steering_blocked = False
                    corner_counter += 1
            if is_obstacle_race and steering_blocked and not steering_blocked2:
                if distance_nearest_obstacle != 0 and 550 > nearest_obstacle_x > 250:
                    steering_end_time = time.time()
                    print("Steering stopped (obstacle)")
                    steer_forward()
                    backward(speed)
                    time.sleep(0.5)
                    forward(speed)
                    has_increased = False
                    has_decreased = False
                    steering_blocked = False
                    corner_counter += 1
            
            # Driving around obstacles
            if distance_red != 0 and nearest_obstacle_color == "red" and distance_right > 25 and not steering_blocked and avoiding_allowed and red_obj_x > 200 and distance_red < 600:
                avoiding_duration = 0.5
                if (time.time() - steering_end_time) >= 0.5:
                    longer_countersteering = True
                else:
                    longer_countersteering = False
                print("Now correcting right (red obstacle)")
                steer_forward()
                backward(speed)
                time.sleep(1.2)
                forward(speed)
                time.sleep(0.2)
                steer_right()
                time.sleep(avoiding_duration)
                steer_forward()
                time.sleep(avoiding_duration / 1.4)
                if not just_stopped_corner_turn_because_of_obstacle:
                    steer_left()
                    if longer_countersteering:
                        time.sleep(avoiding_duration / 1.25)
                    else:
                        time.sleep(avoiding_duration / 100)
                    steer_forward()
                just_avoided_obstacle = True
                just_avoided_obstacle2 = True
                avoiding_end_time = time.time()
                avoiding_distance = distance_red
                avoiding_color = "red"
            if distance_green != 0 and nearest_obstacle_color == "green" and distance_left > 25 and not steering_blocked and avoiding_allowed and green_obj_x <600 and distance_green < 600:
                avoiding_duration = 0.5
                if (time.time() - steering_end_time) >= 0.5:
                    longer_countersteering = True
                else:
                    longer_countersteering = False
                print("Now correcting left (green obstacle)")
                steer_forward()
                backward(speed)
                time.sleep(1.2)
                forward(speed)
                time.sleep(0.2)
                steer_left()
                time.sleep(avoiding_duration)
                steer_forward()
                time.sleep(avoiding_duration / 1.4)
                if not just_stopped_corner_turn_because_of_obstacle:
                    steer_right()
                    if longer_countersteering:
                        time.sleep(avoiding_duration / 1.25)
                    else:
                        time.sleep(avoiding_duration / 100)
                    steer_forward()
                just_avoided_obstacle = True
                just_avoided_obstacle2 = True
                avoiding_end_time = time.time()
                avoiding_distance = distance_green
                avoiding_color = "green"
            
            just_stopped_corner_turn_because_of_obstacle = False
            
            if (distance_green != 0 and nearest_obstacle_color == "green" and distance_green < 350 and green_obj_x < 600) or (distance_red != 0 and nearest_obstacle_color == "red" and distance_red < 350 and red_obj_x > 200):
                steer_forward()
                backward(speed)
                time.sleep(0.6)
                forward(speed)
                just_avoided_obstacle = True
                just_avoided_obstacle2 = True
                avoiding_end_time = time.time()
                if steering_blocked:
                    steering_end_time = time.time()
                    steer_forward()
                    print("Steering stopped")
                    has_increased = False
                    has_decreased = False
                    steering_blocked = False
                    steering_blocked2 = False
                    just_stopped_corner_turn_because_of_obstacle = True
                    corner_counter += 1
                backward_time = time.time()
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

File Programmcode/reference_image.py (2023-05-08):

import cv2 as cv

# Initialising camera
cap = cv.VideoCapture(0)
if not cap.isOpened():
    print("Cannot open camera")
    exit()

while True:
    # Reading camera frame
    success, frame = cap.read()
    if not success:
        print("Can't receive frame. Exiting")
        break

    # Displaying camera frame
    cv.imshow("Reference Image", frame)

    # Saving image as "referenceImage.png" when "a" is pressed
    if cv.waitKey(1) == ord("a"):
        print("pressed a")
        frame = cv.imwrite("/home/pi/Desktop/referenceImage.png", frame)
        break

cap.release()
cv.destroyAllWindows()

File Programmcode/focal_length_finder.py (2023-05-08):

import cv2 as cv
import numpy as np

# Defining the real distance and height of the object in the reference image
known_height = 100
known_distance = 270

# Creating arrays with the lower and upper HSV limits
lower = np.array([52, 122, 87])
upper = np.array([89, 244, 255])


# Function to calculate the focal length of the camera
def focal_length_finder():
    focal_length = (reference_image_obj_height * known_distance) / known_height
    return focal_length


# Function to find objects within the HSV limits and their height in pixels
def obj_data(frame):
    obj_height = 0
    hsv = cv.cvtColor(frame, cv.COLOR_BGR2HSV)
    mask = cv.inRange(hsv, lower, upper)
    _, mask1 = cv.threshold(mask, 254, 255, cv.THRESH_BINARY)
    contours, _ = cv.findContours(mask1, cv.RETR_EXTERNAL, cv.CHAIN_APPROX_NONE)
    for contour in contours:
        min_area = 600
        if cv.contourArea(contour) > min_area:
            x, y, w, h = cv.boundingRect(contour)
            cv.rectangle(frame, (x, y), (x + w, y + h), (0, 255, 0), 2)
            obj_height = h
    return obj_height


# Reading the reference image and finding the height of the object in pixels in the reference image
reference_image = cv.imread("reference_image.png")
reference_image_obj_height = obj_data(reference_image)

# Calculating and printing the focal length of the camera
focal_length = focal_length_finder()
print(focal_length)
